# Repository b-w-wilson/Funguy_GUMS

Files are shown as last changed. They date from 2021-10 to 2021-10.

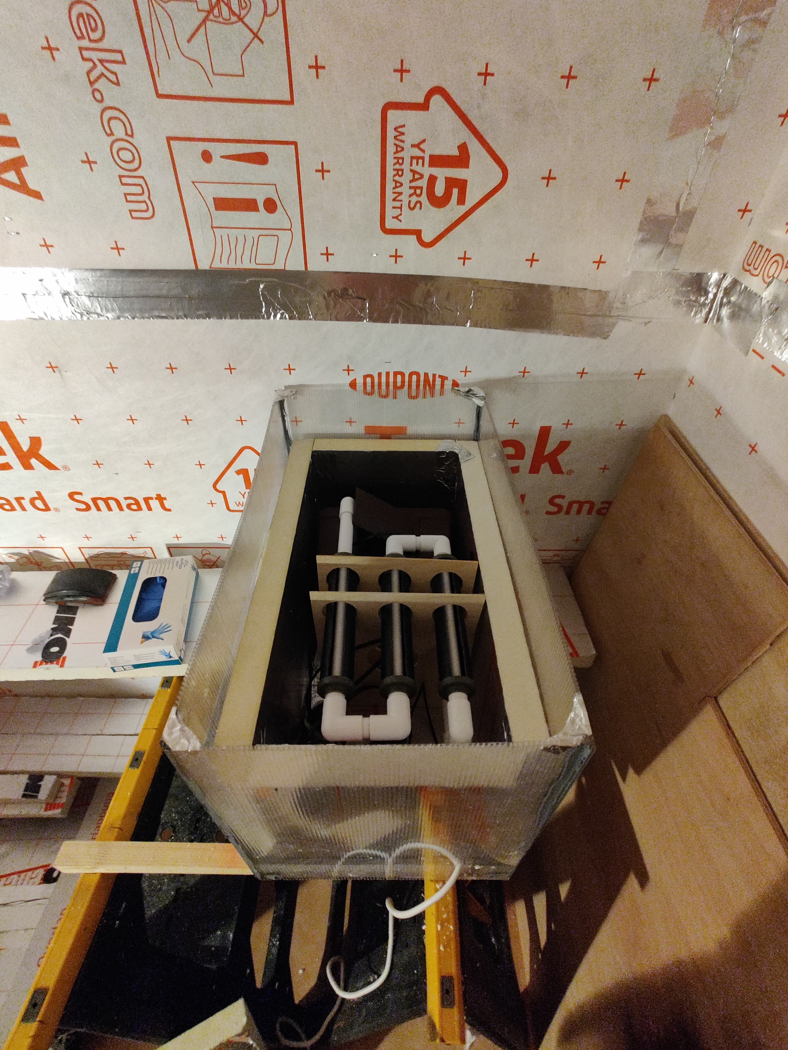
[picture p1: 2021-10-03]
Build/IMG_20211003_214133.jpg

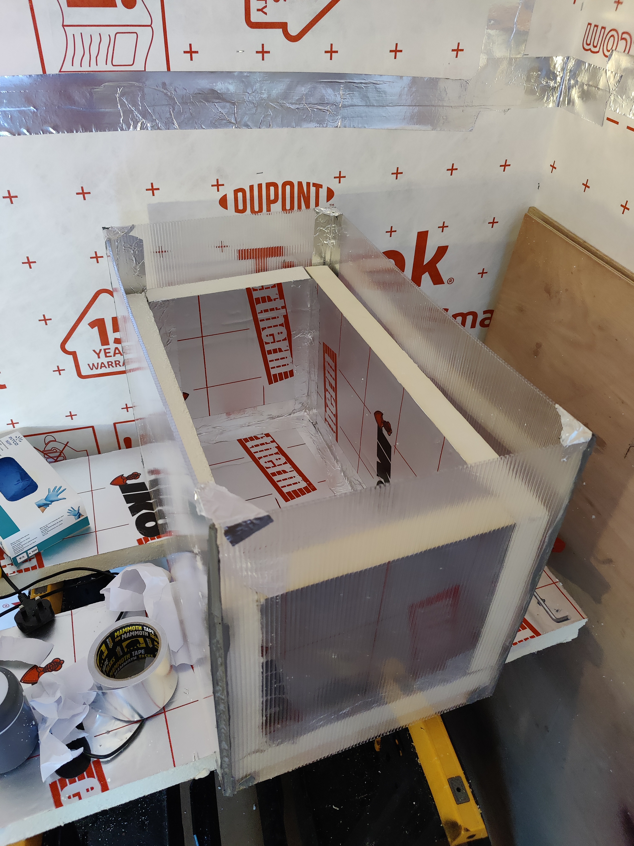
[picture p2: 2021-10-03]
Build/IMG_20211003_183508.jpg

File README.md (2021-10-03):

# Funguy_GUMS
Team Funguy final project for the 2021 NASA Space Apps Challenge Hackathon

## Exploring the solution:
* Our main solution is the "**Methods**", "**Introduction**", "**Improvements**", and "**Abstract**" documents, alongside all files in the **Build** directory.
* A CAD model was also created, with pictures in the "**CAD**" folder.
* The "**Diagrams**"" folder contains diagrams to show how our system build will work.
* References can be found in the respective "**References**" directories.
* Research conducted to create the final solution document and the build is contained in the "**Technical Design Research**" directory.
* The "**Assets**" folder contains all logos, images, or otherwise promotional material created.

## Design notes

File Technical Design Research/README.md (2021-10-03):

# NOTE:
This folder contains raw research from sources listed in our references. This is material which we used to build the actual project contained within the introduction, methods, and in the build of our system.

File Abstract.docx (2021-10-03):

GUMS: Growth Unit for Mushrooms in Space is an ingenious mushroom growing hybrid system consisting of an electromagnetically treated homogeniser for nutrient mixing and solution sanitising and hydroponic porous ceramic tubes for the nutrient delivery and recycling. The growing environment will be monitored via an autonomous sensor system, which transmits the air sensing (air temperature, relative humidity, light intensity) and water sensing (solution temperature, pH, electrical conductivity, concentration of nutrients) data to a mobile app.

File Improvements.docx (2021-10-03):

Overall, Space Apps Challenge has been a unique experience in which we have had the opportunity to grow both personally and professionally!

Over the weekend and the month prior to the challenge, we have planned out as much as possible our GUMS system and have tried to get a basic mycology background in order to better understand how mushroom growth in hydroponics based systems. We are looking forward to continuing the development by adding the additional subsystems to the main porous tube nutrient delivery system. We believe that the solution we have came up with will certainly make a difference not only in long distance space travel, but also on Earth.

Overall development of the project started with planning stage. We started with initially coming up with a few ideas of projects that we could work on, and after brainstorming some ideas around hydroponics and tomato/lettuce growth, ordered pizza. Rebeca ordered a pizza with mushrooms on it, to which Bruce responded by voicing his dislike for mushrooms. Rebeca asked what Bruce would do if he was stuck somewhere and all there were to eat were mushrooms, to which Bruce responded, “hmm.. well we could use our hydroponic system to grow mushrooms”, and there we are. With the decision made, we spent a few weeks doing background research, ensuring that on the weekend of the hackathon, we could put together our report, and build the system from scratch. Alongside this, we placed any orders of hardware or parts that they would arrive for the weekend.

On the weekend of the hackathon, we started bright and early at 9am beginning the build. First creating the growth tubes (connector ends, black ABS tube, ceramic tube), then connecting them together to the pump and nutrient tank. With a quick trip to B&Q to pick up some extra sealant and pipe 90 degree turns, this system was mostly complete, with a few worries about leaks due to how quickly it had been put together. Then on day two, the wooden base was built, along with finishing touches to the tube system. The polycarbonate encasement alongside PIR insulation was then constructed around the box, ensuring that all gaps were sealed shut with aluminium tape. Nearing the end of day two, we recorded the walkthroughs and turning on of the pump for the first time.

Our biggest challenge was faced with the heating element. Our original plan called for a 2L cola bottle to be cut and an aquarium heater placed inside, however it proved too difficult to seal once it had been opened. With some other attempts with plastic bags, cut parts of a tube, and a trip to Tesco to quickly by a cereal container in a last-ditch attempt. Unfortunately we were unable to get the heater working and in a safe, sealed environment by the end of the hackathon. Alongside this, our fears were met with reality with a few small leaks from the tubes upon the pump being ran for a few minutes. We will drain the system and fix the leaks with epoxy.

Overall, we were very content with what we have been capable to build, considering how quickly it was manufactured. It was greatly aided by the 3D printed pipe connectors and fast drying epoxy/solvent cement. While we have bought the substrate and mushroom spores in a syringe, we have yet to put the substrate in the tubes. This was due to the leaks appearing and lack of time near the end of the weekend. We fully intend on still attempting to use the system in the coming weeks.

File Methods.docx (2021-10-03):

### Growing mushrooms in space

GUMS: Growth Unit for Mushrooms in Space is an ingenious mushroom growing hybrid system idea consisting of an electromagnetically treated homogeniser for nutrient mixing and solution sanitising and hydroponic porous ceramic tubes for the nutrient delivery and recycling. The growing environment will be wirelessly monitored via an autonomous sensor system, which transmits the air sensing (air temperature, relative humidity, atmospheric gases concentration, light intensity) and water sensing (solution temperature, pH, electrical conductivity, concentration of oxygen and nutrients) data to a mobile app. Further improvements would include a treatment and dehydration stations.

Our GUMS design has been inspired by NASA’s PTPNDS system. In 2003, T.W. Draschel has published in NASA Technical Memorandum the technical design of a device which utilises a loop to control the delivery of water and nutrients to the roots of super-dwarf wheat and, subsequently, to prevent the anoxic effects experienced by plant rhizospheres in conditions of microgravity. According to the paper, eight porous ceramic tubes with a diameter of 2 cm and 80 cm length are connected to a magnetically coupled impeller at the upstream end and to a peristaltic pipe at the downstream end. These tubes are fed by a 80 litres nutrient tank attached to the upstream end whereas the solution is removed out of the system and recycled at the downstream end. Metal-halide lamps provide the necessary active radiation for photosynthesis and a bracket system is attached to diffuse the liquid nutrient solution under pressure.

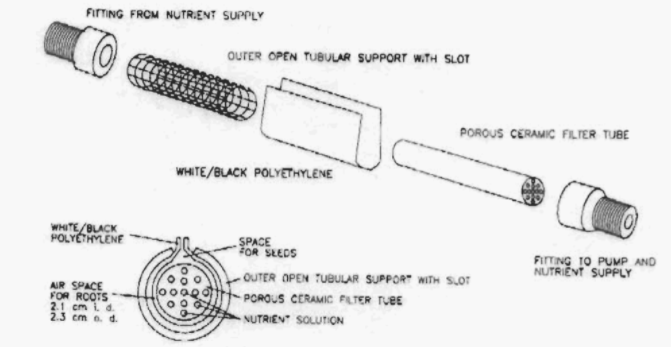
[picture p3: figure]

Fig 5: Scheme of Porous Tube Plant Nutrient Delivery System (T.W. Draschel, “DEMONSTRATION OF A POROUS TUBE HYDROPONIC SYSTEM TO CONTROL PLANT MOISTURE AND GROWTH”, NASA Technical Memorandum 2004-21 1533, October 2003)

The outline of the system is further developed by the Department of Bioresource Engineering of McGill University, Canada, in order to make it functional for mycelium and mushroom production. GUMS is a modified version of this model which uses an alignment of three porous ceramic tubes, each of 15 mm in outer diameter, 10 mm in inner diameter and 200 mm in length, rather than only one, making the system more suitable for much smaller space. If the growing chamber of McGill University’s porous tube plant for nutrient delivery system needs a 1.09 m in length, 0.59 m in width and 0.52 m in length container for the assembly, GUMS only uses 60 cm in length, 35 cm in width and 40 cm in height. Due to the reduced dimensions of the container, GUMS require less energy to be humidified and heated up, which means that we also save energy, and, therefore, money. Besides the continuous monitoring of multiple environmental parameters amongst which some uncommon ones, such as light intensity, pH and electrical conductivity, GUMS makes use of the newest discoveries in the full solution sterilizing treatments to prevent the contamination noticed in McGill University’s system and, subsequently, the pump clogging.

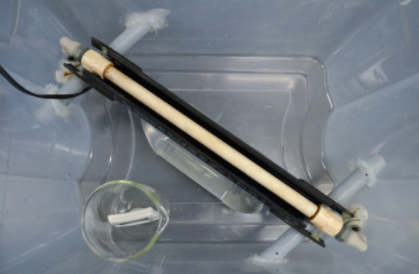
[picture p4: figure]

Figure 6: Nutrient Delivery System seen from above (Prof. Chandra Madramootoo, “Mycelium and Mushroom Production Using a Hydroponic Porous Tube Nutrient Delivery System”, Department of Bioresource Engineering, McGill University, Macdonald Campus, April 2018)

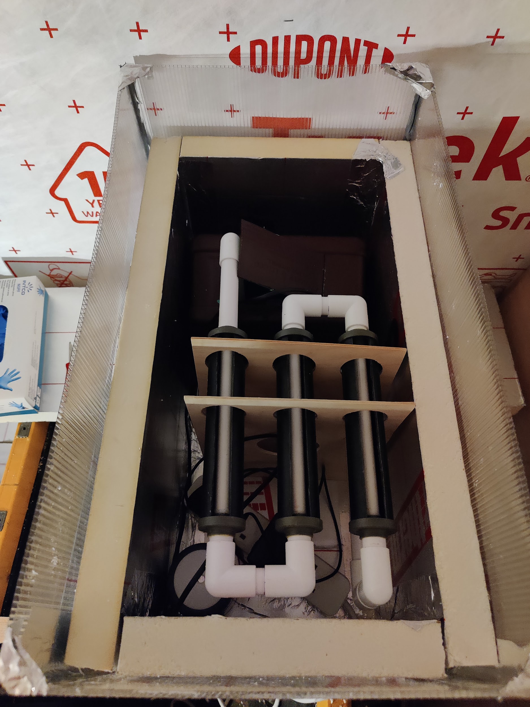
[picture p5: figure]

Figure 7: Nutrient Delivery System seen from above (GUMS design)

### Nutrient delivery system

An inert substrate of organic brown rice flour, vermiculite and gypsum was sterilized and inoculated with a liquid media containing Pleurotus ostreatus spores. The axenic nutrient solution is dispersed into a bed of nutrient free substrate, encased by ABS pipes around the ceramic tubes. The ceramic tubes are, then, joined to a 5L nutrient tank by opaque, PVC pipes. The opacity of the pipes diminish the chances of internal algal contamination. In the nutrient tank, we added a centrifugal submersible pump, attached to the nutrient tank walls using silicon caps. The remaining solution which circulated through the system is transported downstream to the nutrient tank where the consumed nutrients are replenished.

### Nutrient mixing and treatment station

From (Prof. Chandra Madramootoo et al., April 2018), we know that contamination of nutrient and water solution may be an issue, especially during the mixing. From this, we propose a system may be to mix the water and nutrient solution inside a sealed mixing chamber. This will allow for the inlet of nutrients at high pressure to mix directly with the water, creating an even distribution of components.

The homogenization will occur in a venturi space, where mechanical mixers are placed. The surface of the venturi chamber is circularly-ridged to promote further physical and chemical reactions in the aqueous media. The inlets to the chamber of the mixer as well as the nutrient tank include a jacket insulation to keep the temperatures of the liquid solutions below room temperature, and, subsequently, to increase the dissolution of oxygen and nitrogen.

In comparison with other subsystems, the venturi chamber should be treated with maximum care as there are high chances for contamination, despite UV sterilising the water before connecting to the inlet. The risk of contamination can be drastically reduced by utilising EMF solution treatment. EMF has been widely used for centuries to mitigate bacterial contamination, but also to assist the electrocoagulation and advanced oxidation processes. In comparison with electrolysis for which the presence of electrodes in the nutrient solution tank is mandatory, in the EMF treatment technique, solenoid coils are attached in the proximity of the venturi chamber to induce an electromagnetic field of high intensity and less homogeneous waveform in the liquid. Moreover, as electrodes need to be frequently checked and periodically changed, electrolysis is associated with high maintenance cost, which cannot be said about our treatment unit.

### Growth chamber

The growing chamber is our own customised polycarbonate bin, supported on a wooden base, measuring 60cm in length, 35cm in width and 40cm in height. We included the ceramic tubes inside the bin whereas the nutrient mixing and treatment station is kept outside the bin. The openings cut in the polycarbonate sheets to connect the subsystems have been surrounded by flexible silicone adhesive in order to forbid the air flow transfer between the bin and the outer space. The stability of the ceramic tubes is given by plastic fittings. The whole chamber is surrounded in 40mm PIR insulation to trap heat and moisture inside and reduce the energy requirements of the system.

### Heating system

The heating system comprises a 2L soda bottle, partially filled with water in which an aquarium heater is glued with silicone adhesive. The heater has incorporated a thermostat so as we are able to change the temperature to accommodate different growing stages. Currently, as our system is in the mycelial growth stage, we keep the temperature higher, at 25 degrees Celsius and the humidity at 85%.

### Wireless environmental monitoring

To monitor the environment around our system, alongside the environment inside our system, we propose that a series of sensors could be used to monitor all aspects of the fungi growth. This system would be controlled by a central computer, which would receive many inputs from sensors, and output the calculated result to the actuators.

The air parameters FUNGUY decided to monitor are air temperature, relative humidity, atmospheric gases concentration, light intensity. The light is provided by a 4.5W 2700K LED bulb. The state of the nutrient solution is communicated by water sensors, such as the solution temperature, pH, electrical conductivity, and concentration of oxygen and nutrients.

These sensors should be wireless, enabling a clean wire-free connection from inside each individual growth chamber, to the main monitoring computer. Alongside this, the actuators would also be wireless. These actuators would be pump output, humidifier output, heater output, and LED bulb output.

### Modular design

GUMS has been designed to sit on two rails and be rack mounted. At the back of the bin there is a input/output port, allowing for power inside the chamber alongside nutrient solution to be filled. If for any reason a GUMS unit fails, it can be quickly swapped out with a functional unit to ensure that enough food is continuously being grown onboard the craft. A system failure would automatically be noticed by the wireless environment monitoring, and personnel would be notified via the mobile app that a unit has malfunctioned.

### State Machine Diagram

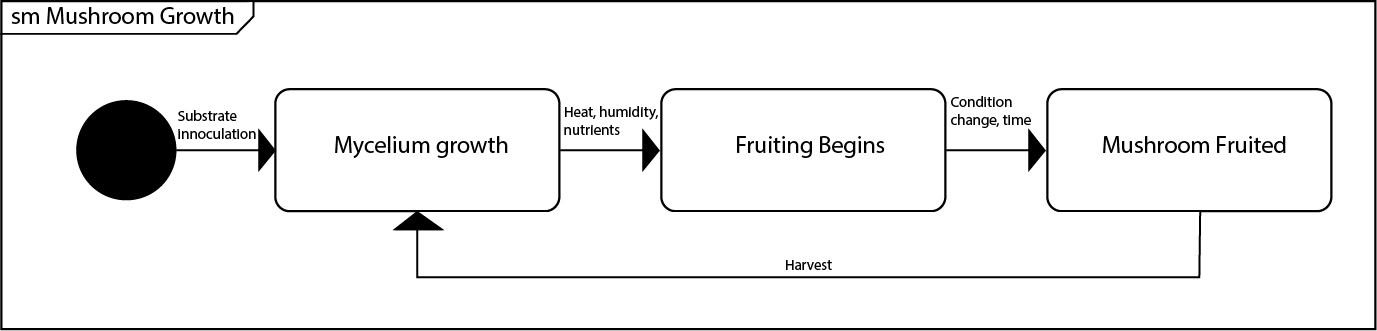
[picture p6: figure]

## System Architecture

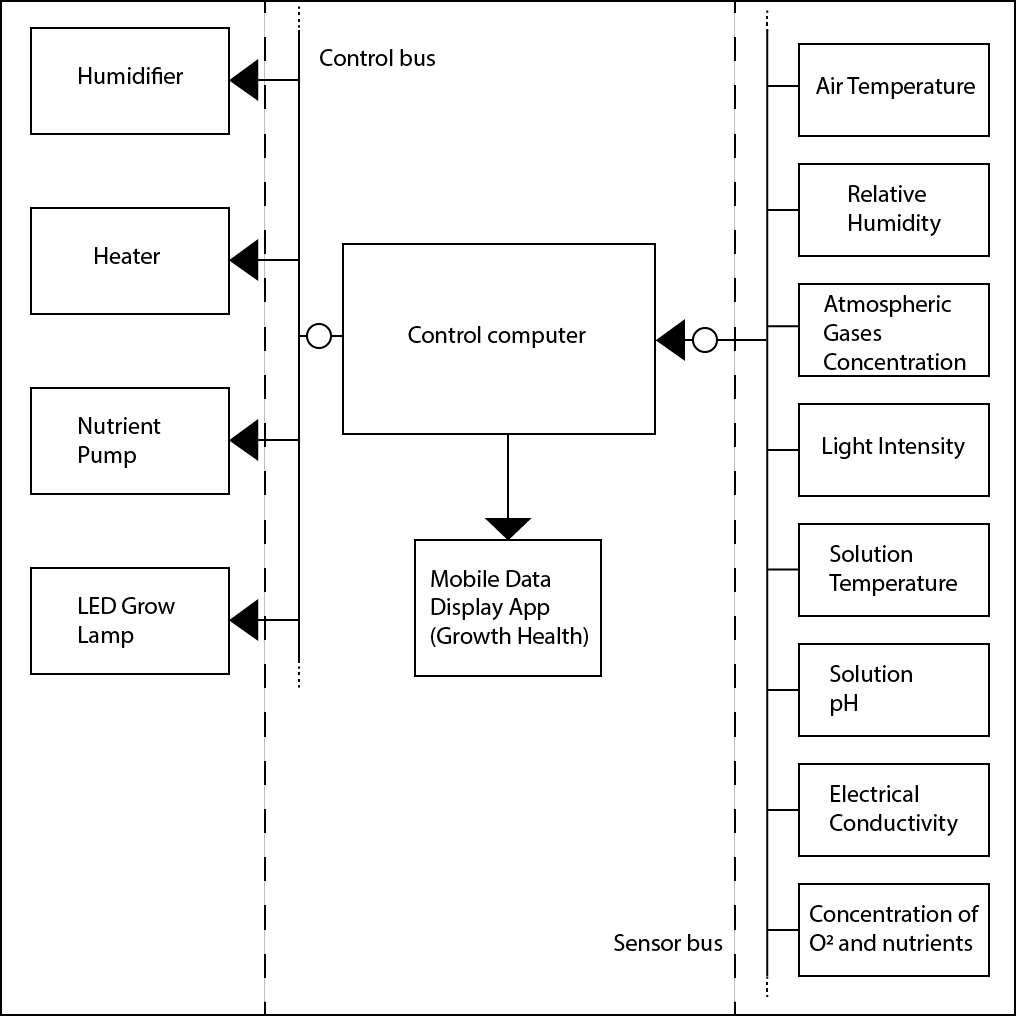
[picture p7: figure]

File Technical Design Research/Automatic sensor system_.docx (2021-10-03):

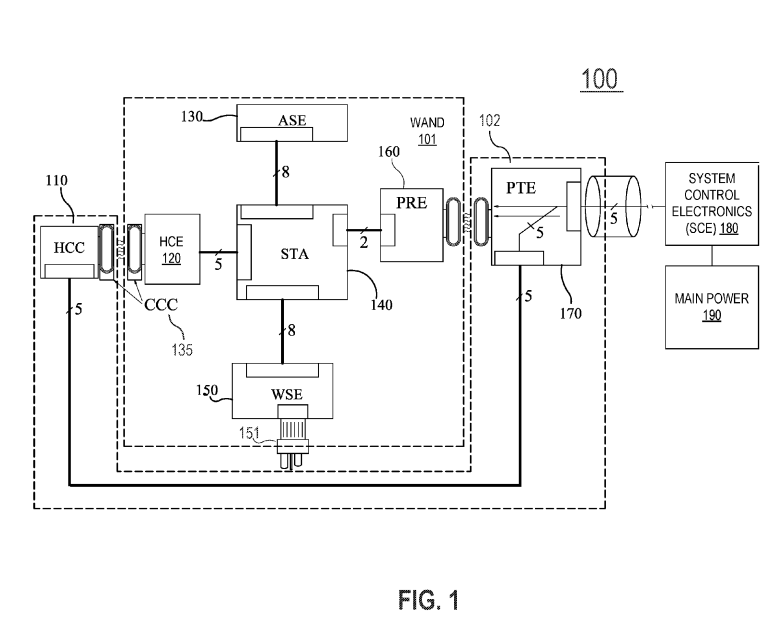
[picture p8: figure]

101 = WAND

102 = collar

120 = H-Field Communications Electronics (HCE)

130 = Air Sensor Electronics (ASE)

140 = Station Board (STA)

150 = Water Sensor Electronics (WSE)

160 = Power Receiver Electronics (PRE)

110 = H-Field Communications Collar (HCC)

170 = Power Transmitter Electronics (PTE)

- PTE employs power, ground, and data lines connected to System Control Electronics (SCE)

190 = main power supply

- power supply may be or connect to a line Voltage from a power company and may be transformed or rectified in different ways to power SCE and other Subsystems
- SCE and main power supply may connect to WAND, for example, to communicate information through with or through WAND and collar system
- PTE in an exemplary implementation provides power to PRE, which may be inside a housing of WAND, and PRE distributes power within WAND to HCE, ASE, STA, and WSE

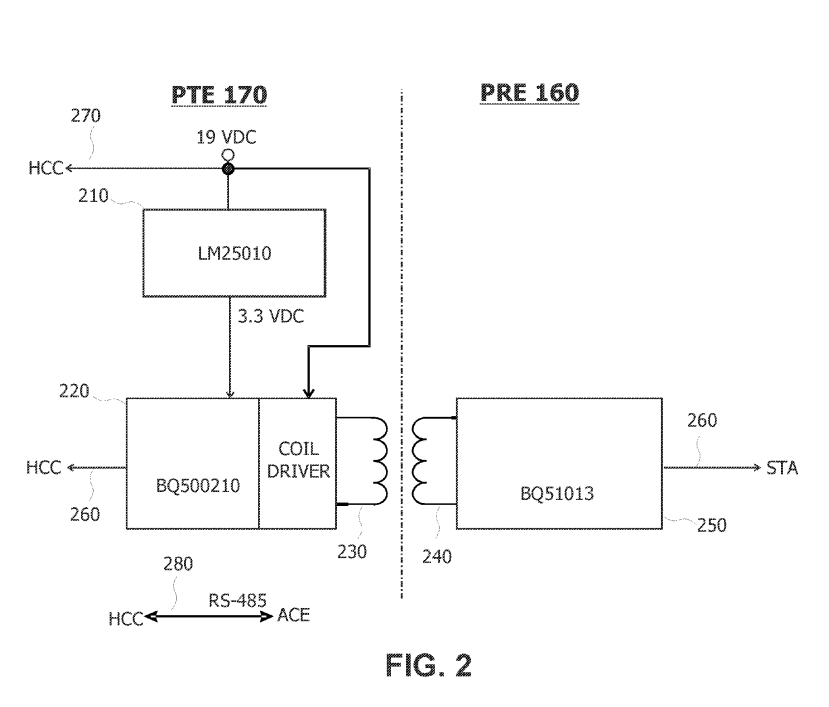
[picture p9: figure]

210 = regulator

- receives 19 VDC from an external supply
- provides a 3.3 VDC output to power a manager

220 = manager (eg Texas Instruments P/N BQ500210 “Qi Compliant Wireless Power Transmitter Manager )

- provides a pulse width modulation (PWM) drive signal to a high speed coil driver (eg Texas Instruments TPS28225) which in turn drives a transmitting coil

230 = Wurth Wireless Power Charging Transmitter Coil

- Uses 19-VDC supply
- In the proximity of a receiving coil

240 = receiving coil (eg TDK P/NWR-483250)

- electrically connected to a Texas Instruments BQ51013 Wireless Power Receiver

250 = Texas Instruments BQ51013 Wireless Power Receiver

- 5.0 VDC output of the power receiver may be provided to STA 140 on a line 260

5.0-VDC power received by STA 140 from PRE 160 on line 260 is further provided directly to the HCE 120 on a line 343, WSE 150 on a line 342, and ASE 130 on a line 341. 5.0 VDC power is converted to 3.3 VDC and provided to a Wi-Fi unit

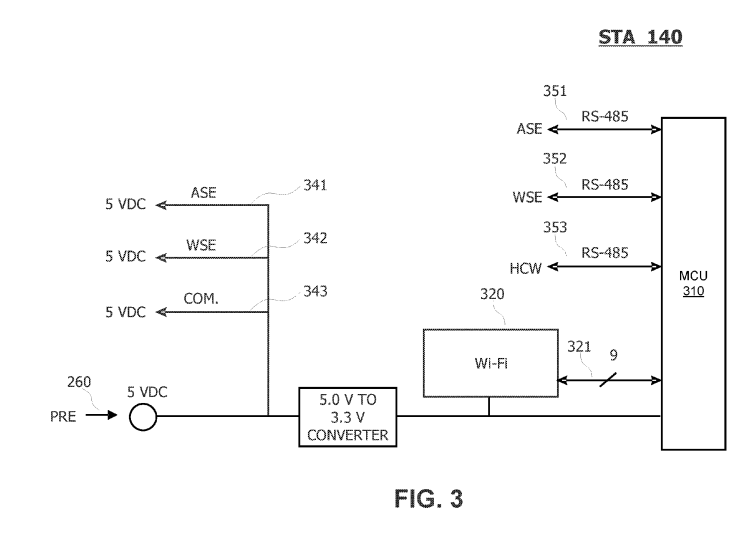
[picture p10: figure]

320 = Wi-fi unit (eg a Microchip MRF24WGOMA)

- responds to data and commands provided by a microcontroller unit

310 = microcontroller unit (eg Microchip PIC32MX695F512L)

STA 140 may also include RS-485 communications capability between MCU 310 and ASE 130 on a bus 351, WSE 150 on a line 352, and HCE 120 on a line 353.

ASE

- STA 140 may connect to ASE 130, which may support a Suite of sensors for sensing characteristics of the environment of a growing plant. In addition to power and ground on line 341, STA140 may have an RS-484 communications for wire, two-way communication with ASE 130 via bus 351.
- sensors that measure concentrations of CO, CO. and O in the atmosphere around a plant and sensors that measure characteristics of the ambient light in the environment.

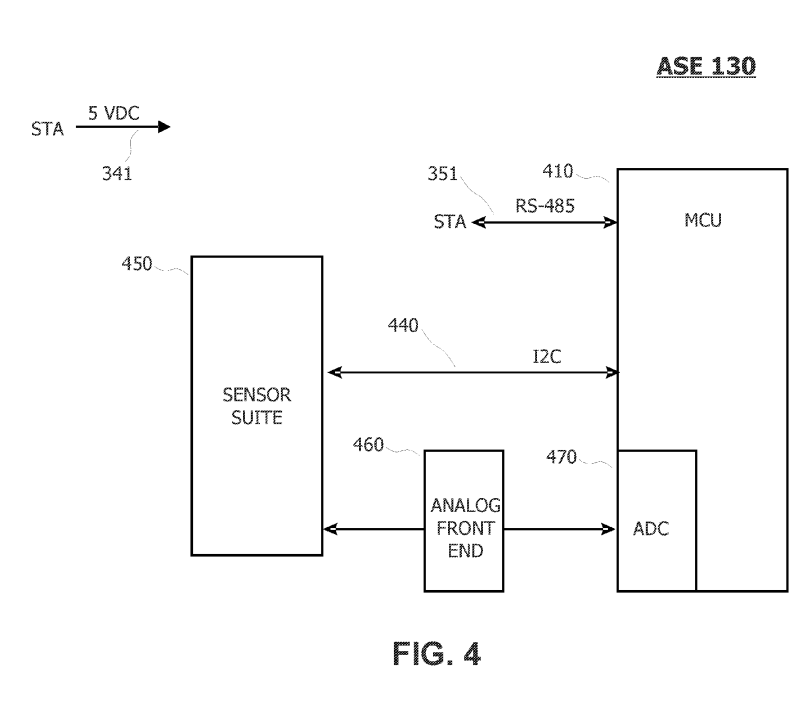
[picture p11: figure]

- ASE 130 may include an MCU 410, for example, a PIC32MX350F256H microcontroller, wherein MCU 410 includes an analog-to-digital converter (ADC) 470
- MCU 410 may manage the sensors, for example powering them up or down, placing one or more sensors in standby or operative mode, determining the status of one or more sensors, or performing diagnostics on one or more sensors.
- MCU 410 may also be programmed to receive requests for data related to a given sensor and to provide the data back to STA board 140 via the RS-485 bus 420
- STA 140 may then provide the data to the requester via the Wi-Fi unit 320 or another data link.

WSE

- Principle of working identical to ASE 130
- Examples of sensors include any c combination of pH sensors, temperature sensors, total dissolved solids (TDS) sensors, sensors of specific chemicals, resistivity sensors, and any other sensors useful for sensing one or more characteristics a nutrient Solution in a hydroponic system

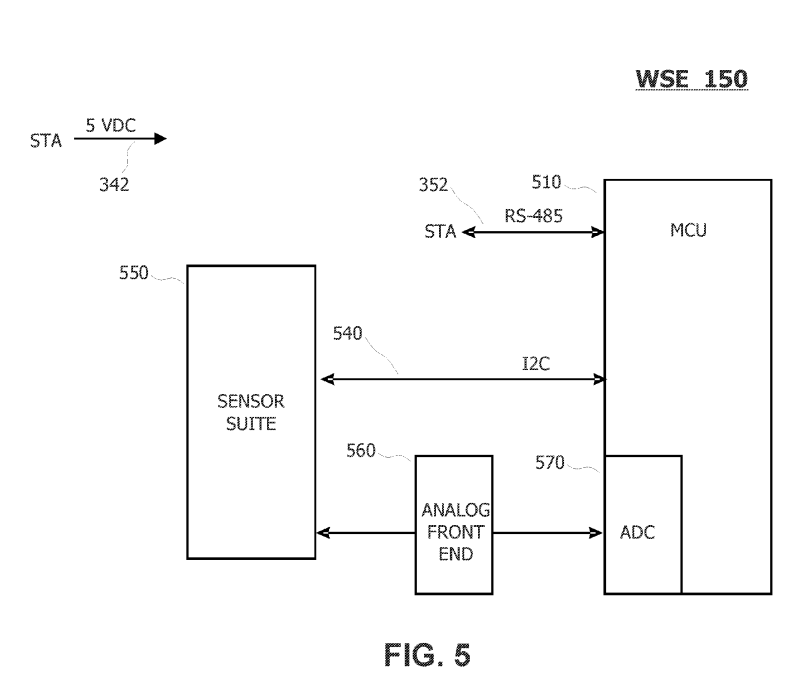
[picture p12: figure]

HCE

- HCE 120 and HCC 110 operate in a similar fashion to PTE 170 and PRE 160, except data is exchanged between the transmitting and receiving coil rather than power.

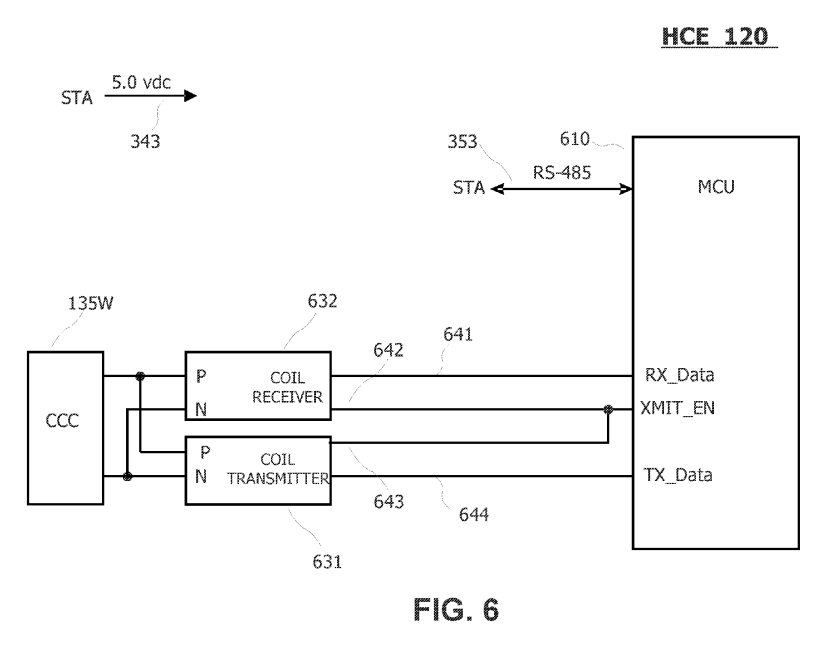
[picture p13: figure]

- MCU 610, for example, a Micro chip PIC32MX350F128D, may communicate with STA 140 via the RS-485 bus 353.
- MCU 610 receives data on a line 641 and sends data on a line 644.
- Data activity is controlled by an enable signal XMIT EN on a line 642, 643.
- signals connect MCU 610 to a coil transmitter 631 and a coil receiver 632.
- P and N signals from the coil transmitter 631 and the coil receiver, connected to drive a coil, e.g., a CCC

CCC 135W coil interacts with a matching (may be identical) coil CCC 135C on HCC 110, the pair of coils being proximate to enable inductively passing data signals when the WAND is inserted for operation.

HCC

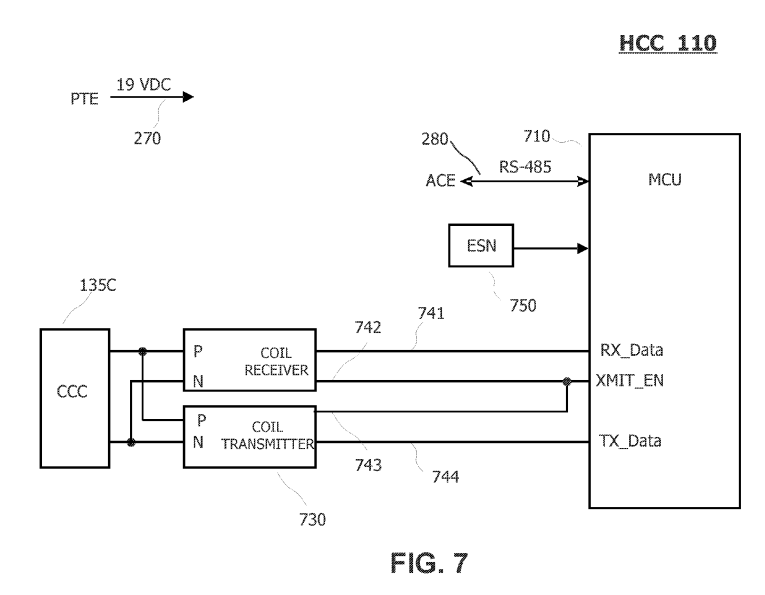
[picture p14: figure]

- Similar in working as HCE
- communicate with SCE 180 via the RS-485 bus 280
- HCC 110 includes an ESN (electronic serial number) (eg a Maxim Integrated DS2411)

SCE

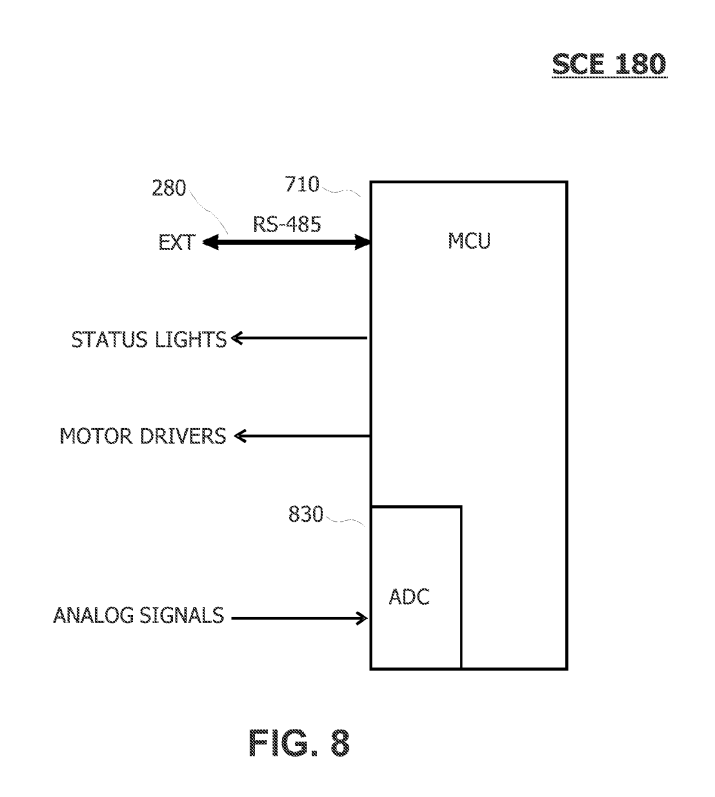
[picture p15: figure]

- communicate with WAND 101 via HCC 110 on an RS-485 bus 280
- include an MCU 810, which includes a number of general purpose input/output (GPIO) pins 820.
- include an ADC 830 to provide a digital version of analog signals connected to the ADC 830
- MCU 8.10 may provide signals to turn fans ON or OFF, and turn on a light of an appropriate color
1. Implementation of network station
- includes a microcontroller 1210 that may be programmed for desired communications among sensor modules 1130 and 1150, system control 180, and through a network to a remote device
- controller 1210 may execute software or firmware to collect data points from ASE module 1130, WSE module 1150, or system control electronics 180, to upload the data points to a remote device or cloud database, and to provide system control electronics 180 with the data points or with data, commands, or instructions received from a wireless network.
- Controller 1210 connects to an ASE interface 1230, which may be a chip or other electrical circuit that implements a signaling protocol to transmit or receive communications with ASE module
- ASE interface 1230 may be RS-485 compliant and may connect to ASE module 1130 through a connector 1232

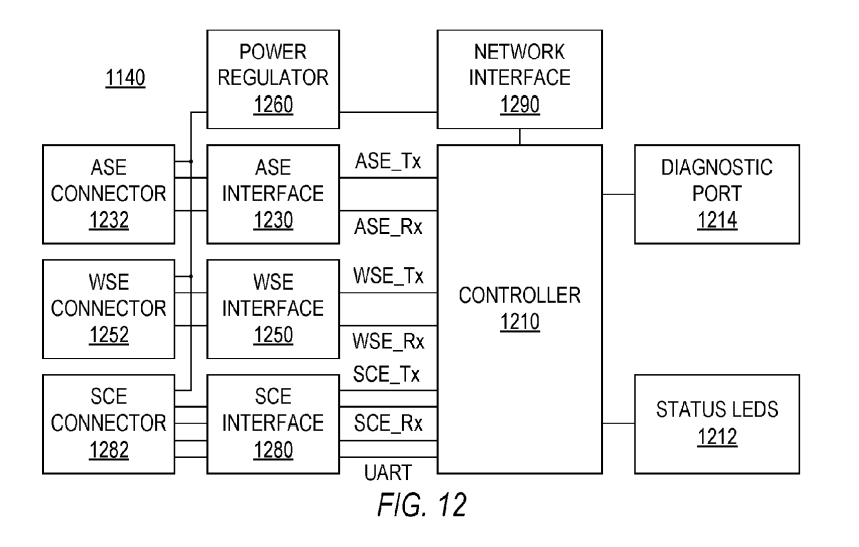
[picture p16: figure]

- controller 120 connects to WSE interface 1250 and SCE interface 1280, which respectively allow wired communication with WSE module 1150 and system control electronics 180 through respective connectors 1252 and 1282
- power regulator 1260. which provides power to controller 1210 can also provide power or receive power via connectors 1232, 1252, and 1282 to ASE module, WSE module 1250, and system control electronics
- A network communication interface 1290 may be a chip or electronic circuit that implements a wireless protocol, e.g., Wi-Fi, that enables network device 1140 to communicate through a wireless network
2. Implementation of sensor electronics
- includes a controller 1310 that may be programmable to operate, receive measurements from sensors, and transmit the measurements to network station 1140.
- sensors 1350 may be able to digitally communicate with controller 1310 or may provide analog measurement signals to an analog frontend 1352 that converts the analog signals to digital signals suitable for controller 1310.
- Controller 1310 may communicate information such as sensor measurements to network station 1140 through an interface circuit 1340 such as an RS-485 compliant interface chip connected to network station 1140 through a connector 1242
- power regulator 1360 is used in the implementation to receive power through the connector and to supply regulated power in ASE module 1130.

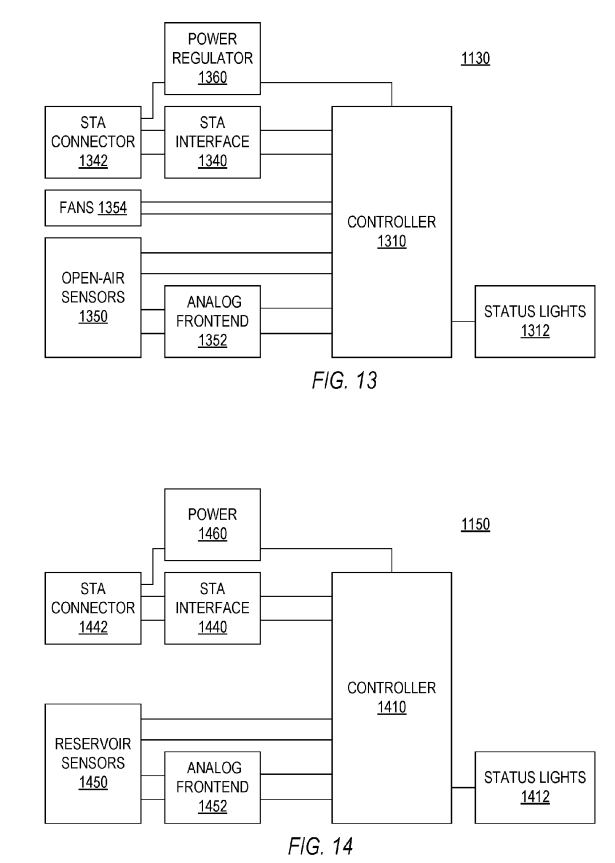
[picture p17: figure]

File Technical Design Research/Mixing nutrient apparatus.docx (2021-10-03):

1. HYDROPONICS APPLICATIONS AND ANCILLARY MODIFICATIONS TO A POLYPHASIC PRESSURIZED HOMOGENZER
a) Introduction
- Ancillary embodiments and modifications to a homogenizer unit (“PPH'), and methods of use directed to hydroponics.
- The apparatus includes a homogenizer body, one or more nutrient stream inlets, one or more water inlets, a mixing Zone where the water stream is commingled with the nutrient stream, and a venturi within the body immediately down stream from the mixing Zone such that the commingled streams are pulled into the Venturi resulting in homogenization.
- The PPH components are insulated to maintain the aqueous nutrient Solutions cooled, below ambient temperature.
- The resulting aqueous nutrient solution can be conveyed in its cooled State to roots of hydroponically grown

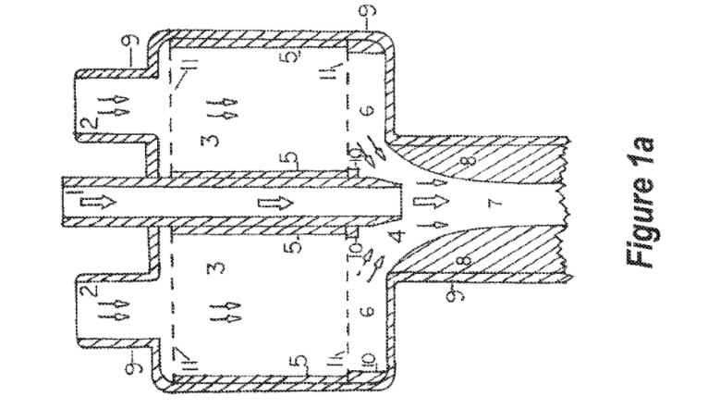
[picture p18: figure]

b) Description
- modified homogenizer unit includes an integrated unit having a much expanded housing that is intended to contain a replaceable ante-mixing chamber containing various packings, baffles, and/or sorbents.
- The housing (9) also has top mounted ports.
- The central port (1) is dedicated to the input of water or a similar solvent mixture.
- One port or several ports (2) is/are dedicated to entry of a gas, gases, liquid, liquids, any type of particle or mixture of particulates that will pass through the port, the ante-mixing chamber or mixing chamber,
- The components are numerically identified as it follows:
1) water or other solvent intake port and jet or nozzle
2) pollutant stream port or ports
3) ante-mixing chamber
4) mixing chamber
5) ante-mixing chamber housing
6) lateral extent of mixing chamber
7) venturi throat
8) Venturi
9) homogenizer housing
10) ante-mix chamber support
11) ante-mixing chamber screen Supports.
- Headspace modifications or embodiments may include a mechanical mixer, mounted on a shaft, driven by an electric motors
- The solution enters the headspace region by one or more ports by passing through a perforated bulkhead, that is mounted within the homogenizer housing
- A single transfer tube or line allows for passage of a solution into the headspace of the homogenizer
- Mixing may be done by a mechanical mixer or by casual mixing while flowing into the ante-mix chamber. This port(s) may be positioned on the homogenizer housing or one or all intake ports other than water
- ante-mix chamber may be cylindrical in structure and fit tightly within the ante-mixing chamber and directly superior to the mixing chambers of the homogenizers
- ante-mixing chambers depicted include the exterior housing, the interior housing the top and bottom support screens
- ante-mixing chambers are Supported both laterally and centrally by circular ante-mixing chamber Supports
- perforations in the upper and lower screens of the ante-mixing chambers may have a variety of designs ranging from hexagonal, circular, square, to diamond-shaped
- These perforations allow for circulation of gas through them while containing and Supporting the various packings within the chambers
- These packings are varied in configuration and may be Bioballs or any other similar configuration, baffles, having any configuration, cross-section, and Surface treatment
- Water and a solvent or solvents containing water and another reactive chemical is delivered to the mixing chamber by a jet or jets
- homogenizer unit mixing chamber is positioned between the jet(s) and above the Venturi(s) of the homogenizer unit(s)
- Although the boundaries of this mixing chamber are not well-defined, this region is the uppermost area wherein the solvents begin to mix before entering the throat
- It is within the venturi that the solvents come into intimate contact with each other
- smooth venturi surface is one option, while a circularly ridged or grooved surface, a surface with vertical vanes allows for furthering certain reactions, and a radially-grooved surface can be used.
- Mixture continues in the retention chamber which may have a series of spherical chambers, be baffled, have a centrally located spiral conduit, or the serial spherical chambers may have a centrally-located spoiler ball or bead
- the extreme lower end of the retention chamber has four, equi-spaced lateral discharge ports.
- These ports can be produced into tubular form, or continued on to form a j-tube
- result in the increase of safety margins by containing the chemical and physical reac tions within an aqueous medium, thereby both containing out-gassing and heat generation from exothermic reactions while also cooling any such reaction by rapidly diluting the reactantS.
- One embodiment is directed to apparatus and methods that may be employed for introducing nutrients into a water stream to provide an aqueous nutrient Solution for hydroponics plant growth
- Such a PPH apparatus may be any of those configurations described herein, and in one embodiment may further include an insulated jacket around Such components as the inlets, the ante-chamber, the venturi, and the outlet to maintain the nutrient solution at temperature below ambient temperature so as to increase dissolution of oxygen, nitrogen, or both into the aqueous nutrient solution. Where a retention chamber is provided within the PPH, it of course may also be insulated.

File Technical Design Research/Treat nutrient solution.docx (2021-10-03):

1. ELECTROCHEMICALLY TREATED NUTRENT SOLUTIONS
- Nutrient compositions with preservative properties are of great need for a variety of agricultural applications, such as,for example, hydroponics where oxygen deficient media results in favorable conditions for undesirable microbial growth, as well as for pre-harvest and post-harvest crop maintenance.
- However, it is critical that the preservative constituents of the composition do not interfere with plant growth, development, and/or quality.
- Free oxygen radicals, for example, which may have biocidal activity, can underlie basic plant signaling and stress responses
- invention provides nutrient compositions that are oxygen-enriched, and potassium-based.
- In literature, the nutrient composition comprises a solution that is generated through electrochemical treatment of potassium chloride or a combination of potassium chloride (KCl) with potassium or sodium carbonate or bicarbonate (KCO, NaCO, KHCO, NaHCO), or other carbonate salt, and/or potassium phosphate(s).
- feed solution may be processed through an electrolytic cell to produce an electrochemically-treated solution
- The solution produced by electrochemical treatment has a predetermined salinity level, pH and concentration of oxidants measured as free available chlorine
- the nutrient composition or solution is used to support hydroponic plant growth.
- for example, the nutrient solution either alone or in combination with other active ingredients are cycled continuously or intermittently through a hydroponics system. The disease protection and/or enhanced plant growth, development and/or health realized by using the compositions and methods of the present invention may lead to improvements in plant performance including but not limited to obtaining greener plants, greater yield, better standability, less root lodging and/or less fruit rotting.
- invention provides a method for preparing the oxygen enriched potassium-based nutrient solution or composition for supporting plant or crop production.
- The method involves incorporating carbonate or bicarbonate (as described) into KCl electrolyte for electrochemical treatment, or directly to an electrolyzed solution of KCl comprising hypohalous acid (e.g., HOCl).
a) Description
- provides nutrient compositions that are oxygen-enriched, and potassium-based, and comprise hypochlorous acid and potassium salts
- composition promotes plant or crop growth through various stages of development, and/or reduces or eliminates the risk of airborne and waterborne anaerobic bacteria, as well as mold and fungal diseases
- combination of oxygen and hypochlorous acid pro vides antimicrobial properties to the nutrient composition, and in combination with potassium, induces systemic protection and modifies disease resistance or susceptibility of crops to infections
- composition is based on a solution prepared by electrochemical treatment of a KCl solution with one or more (or all) of KHCO/KCO, NaHCO, KPO KHPO, and KHPO.
- Other electrolytes, or salts may be included as well as additional ingredients desired
- The feed solution may be processed through an electrolytic cell to produce the electrochemically-treated solution.
- A diaphragm-based electrolytic cell, may be used for the electrochemical treatment; however, other electrolytic cells with separated anode and cathode chambers may be employed.
- For example, the Sterilox(R 2200, or SteriloxR 2300 may be used for the electrochemical treatment.
- The solution produced by electrochemical treatment has a predetermined salinity level, pH, and concentration of free available chlorine (AFC).
- As a result of the electrochemical process of KCl alone or with the addition of the salts (as described), diluted (i.e., below 1.5 g/L of total dissolved solids) nutrient solutions with targeted pH and total oxidants, measured as AFC, are produced.
- The solution in certain embodiments, employs a stabilizing amount of a bicarbonate or carbonate of alkali or alkaline earth metal. Such as, for example, Sodium, potassium, calcium, or magnesium.
- the solution is considered stabilized if the amount of AFC does not drop below about 75% of the initial value over a period of about 6 months.
- The nutrient compositions or solutions may be applied bya foliar spray to the plants in the hydroponics system. either separately or mixed together with other active compounds
b) Example
- A mixture of 2 g/l of KHCO and 8 g/l of KCl were used as a feeding electrolyte solution processed through the diaphragm based electrolytic cell. The final nutrient solution had
- a pH 5.8, electro-conductivity 1.88 mS/cm, oxidants content of 500 ppm (measured as available free chlorine), and 208% saturation of dissolved oxygen.

2. LIQUID TREATMENT DEVICE

- A liquid treatment device comprising : two antennae ; an enclosure for holding a liquid including a solvent and a solute ; a generator operatively connected to the two antennae to generate an oscillating voltage in each antenna , wherein each voltage is out of phase with the other to create an oscillating electric - field ; and the liquid in the enclosure being subjected to the electric - field in the presence of a magnetic field to change the chemical and / or physical prop erties of the solute , without the liquid contacting the two antennae .
- agriculturalists often use borewater / groundwater 35 atomic / molecular mass of that solvent or solute ; and sources that contain high levels of minerals such as calcium carbonate , magnesium carbonate , and sodium chloride
- These borewater / groundwater sources may be used to field the water crops or livestock
- However , carbonates precipitate chemical and / or physical properties of the solute , without over time , producing scale, which may clog the irrigation
- deleterious effect of the precipitation is the reduction in concentration of minerals in the borewater for crops to absorb .
- In agricultural industries , mineral nutrients such as calcium , phosphorous , potassium , sulfur , sodium , solute . chlorine and magnesium required for their growth
- Electrolysis has been used to improve the solubility of combined magnetic field . minerals in solution . However , this technique requires the use of electrodes to treat the water .
- This can be difficult to implement as it requires access to the water such as through portholes cut into existing pipes to insert the electrodes into the water .
- Furthermore , the electrodes would have to be monitored and periodically replaced , which increases maintenance cost
- antennae are electrically isolated from the liquid
- the antennae can be wrapped around a pipe containing the liquid to be treated , whereby the pipe electrically insulates the antennae from the liquid
- antennae do not include electrodes that have to contact to treat the liquid
- generator may generate one or more frequencies to target one or more solutes
- The frequency is proportional to the magnetic field strength B
- frequency may be controlled by the generator by first converting mains alternating current ( AC ) to direct current ( DC ) , before generating voltages of particular frequencies .
- As such , the frequencies output by the generator are not a function of the mains AC frequency
- generator may be powered by a DC power source , such as for example , a solar DC power source to generate oscillating voltages
- the frequency of the oscillating voltage in each antenna is a harmonic of the fundamental frequency of a solvent or solute , and is calculated using the cyclotron resonance harmonic formula :

f_(n+1) =(n+1)Bq/(2πm)

,wherein fn + 1 is an overtone of fundamental frequency , B is the magnetic field strength , q is the solvent charge , solute charge or solvent dipole charge , m is the atomic / molecular mass of the solvent or solute and n equals zero or any whole number

- In cases where n = 0 , the cyclotron resonance harmonic formula reduces to the cyclotron resonance formula
- frequency of the oscillating voltage in each antenna may be calculated using the cyclotron resonance formula

f=(Bq)/(2πm)

wherein scalar f is the frequency of the electric field modulation , scalar B is the magnetic field strength , scalar q is the solvent charge solute charge or solvent dipole charge , and m is the atomic / molecular mass of the solvent or solute

- the liquid treatment device may include a power supply , a means of estimating or measuring magnetic field strength and a calculator for calculating an oscillating voltage to generate an oscillating electric field , wherein the generator uses the power supply to generate the oscillating electric field
- means for estimating or measuring a magnetic field strength is a magnetometer
- device may further include a controller for carrying out any one or more steps of : receiving a signal that conveys the magnetic field strength , calculating a frequency of the oscillating electric field based on magnetic field strength , and sending a signal to the generator to generate the oscillating electric field using the power supply
- liquid may be subjected to an agitation force that is a function of electric field strength , magnetic field strength and instantaneous velocity of an included solvent or solute particle
- controller may carry out any one or more steps of : the selecting an agitation force , estimating or measuring a magnetic field strength , selecting a frequency for an oscillating electric field based on the agitation force selected and sending a signal to the generator to generate the oscillating electric field using the power supply
- liquid is subjected to an agitation force calculated using the Lorentz force formula

F = |g|[E+(ν×B)]

where B is comprised of the instantaneous strength and direction of the magnetic field

q is the solvent charge solute charge or solvent dipole charge

E is comprised of the strength and direction of the alternating electrical field alternating at any frequency

v is instantaneous velocity ( comprised of speed and direction ) of an included solvent or solute particle

F is the force acting on a charge q when q moves within coexisting electrical and magnetic field

- the controller may be used for calculating the frequency of the electric field based on the magnetic field strength obtained from the magnetometer
- the calculations using the cyclotron resonance formula or the Lorentz force formula individually made for each solvent, may be used to calculate the agitation force acting on a charge q when q moves within coexisting electrical and magnetic field
- According to the invention , the liquid is subjected to the electric - field in combination with either the vector magnetic field B or scalar magnetic field B , to increase solubility of the solute in the liquid
- The same oscillating voltage frequency may be supplied to each antenna .
- voltage may be generated as a modulated DC wave-form
- voltage may have a sinusoidal or square waveform in each antenna
- magnetic field value in the cyclotron resonance formula or Lorenz curve formula may comprise the Earth’s magnetic field at the treatment location or the summation of all magnetic field sources (including Earth’s)
- Antennas should be in contact with the enclosure in which the liquid is hold
- lowest frequencies used by the liquid treatment may be about fifteen - fold lower than the fundamental cyclotron resonance frequencies for a solute or solvent
- highest frequencies used by the liquid treatment device may be about one - thousand - fold higher than the fundamental cyclotron resonance frequency for a solute or solvent
- antennae have little or no appreciable current flow as the electric - field is generated by creating a voltage difference between the two antennae
- e oscillating electric - field frequency may be between 0.3 Hz to 300 kHz
- voltage waves may be 180 ° out of phase with each other
- oscillating electric - field:

( i ) a first continuous emission

( ii ) a frequency change

( iii ) a second continuous emission that continues for a period ranging from 1 millisecond to 10 seconds

- Frequency shift is followed by a series of additional frequency changes with each new frequency persisting for a period ranging from 1 millisecond to 10 seconds
- liquid treatment device may include a magnetic field coil as a source of magnetic field .
- The magnetic field coil may be a closed coil ( part of a closed circuit ) and generates an electromagnetic field
- voltage in the magnetic field coil is a modulated DC waveform which is in the same phase as the waveform in one of the antennae
- magnetic field coil may be positioned between the two antennae
- magnetic field coil , if present , may be in the form of wires that can be wrapped around a liquid - containing enclosure
- At least some portion of the magnetic field may be oriented perpendicular to the electric - field .
- This may maximise the force generated to aid dissolution of the solutes in the liquid
- magnetic field coil produces a magnetic field having a strength that ranges from 1/100 to 9/ 10 of the Earth's magnetic field strength ( 1 uT to 200 uT)
- generator may employ an algorithm that utilises a set of frequencies in alternating and / or sequential fashion over a period of time

Example

- Growth of lettuce in hydroponics
- Cyclotron resonance formula was used to specify particular frequecies for the LTD , targeting particular solutes and solvent
- Water treated by UV before being added to the solution
- A digital CR frequency generator ( circuit board ) was used to set up a modulated electrical field to treat the hydroponics medium
- During plant growth , the electrical conductivity and pH of each treatment solution was adjusted as required

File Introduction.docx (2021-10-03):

Growing food in conditions of microgravity has been a matter of interest for the scientific community for a long time, mainly because our dream to conquer outer space can only be accomplished if the basic human needs are satisfied.

### Pleurotus ostreatus and its mycological characteristics

Currently, there are at least 12,000 species of mushrooms worldwide out of which 2,000 species are reported as edible and only 35 are commercially cultivated, with Agaricus bisporus being the most popular. In this project, we have decided to cultivate Pleurotus ostreatus by considering the time of growth and the availability of mycelium on the market. Known as oyster mushroom, Pleurotus ostreatus is a common saprophyte species of the basidiomycetes group, one of the two main large divisions which form the subkingdom Dikarya within the fungi kingdom. As the name suggests, the species has an offset, tongue-, spatula-, or oyster-shaped pileus spanning 2-30 cm. The colour of the pileus can vary between different shades of grey. The pileus is supported by a short, whitish, eccentric or lateral stripe, and, therefore, its thickness depends on the stripe arrangement. White or cream lamellae occur on the decurrent hymenium whereas the white to lilac-grey spore print shows 8-12 μm ⨯3-4 μm sized, hyaline spores.

In the natural environment, Pleurotus ostreatus thrives on the living or dead parts of plants in temperate and subtropical forests during autumn and winter times, when the temperatures are up to 15℃. High carbon dioxide concentrations, up to 28% of the volume, stimulate the growth.

### Mushrooms as an ideal source of nutrients

Either on Earth or in space, a balanced nutrition is crucial in providing the organisms the necessary minerals to maintain high energy levels and, subsequently, good health.

Since antiquity, the fructification of higher fungi has been an integral part of the human diet as it is easily seen with the naked eye, picked by hand, and consumable without processing. The reason for which mushrooms are appearing more and more frequently on our plates is because they represent are source of variety of nutraceutical compounds such as polysaccharides (β-glucans), dietary fibres, terpenes, peptides, glycoproteins, alcohols, mineral elements, unsaturated fatty acids, antioxidants like phenolic compounds, tocopherols, and ascorbic acid. Moreover, the bioactive compounds have proven effects on strengthening the immune system and prevention of heart diseases, hypertension, cerebral stroke and cancers. Mushrooms are also known to exhibit antifungal, anti inflammatory, antitumor, antiviral, antibacterial, hepatoprotective, anti-diabetic, hypolipedemic, antithrombotic and hypotensive activities. Depending on the species, varieties, and the stage of development of the fruiting body, the crude protein content of edible mushrooms ranges from 10% to 35% of dry weight (DW). The dry weight recommended to maintain an optimal nutritional balance in a man weighing 70 kg is 100- 200 g.

Mushrooms are richer in proteins than most vegetables. Specifically, the amount of essential amino acids in mushroom proteins ranges from 30 to 50g/100g protein DW, from which the most important ones are glutamic acid (130–240 mg/g protein DW%), aspartic acid (91–120 mg/g protein DW %) and arginine (37–140 mg/g protein DW%). Besides these, the two unusual amino acids γ-amino butyric acid (GABA), a non- essential amino acid, and ornithine, known for their peculiar physiological activities, have also been found. Similar to proteins, the carbohydrate content in the fruiting bodies comprising of monosaccharides (eg sugars), oligosaccharides (eg trehalose and non-starch polysaccharides), and small amounts of sugar alcohol, such as mannitol and trehalose serve as 50 to 65% on dry weight.

In comparison with carbohydrates and proteins, mushrooms are low in lipids (less than 5% DW). With a total lipid content of 20 to 30 g kg-1 DM, mushrooms contain unsaturated fatty acids, such as linoleic and oleic acids and tocopherol. Whereas tocopherol is an important antioxidant, the linoleic acid has been mentioned to exhibit anti-carcinogenic effects on almost all stages of tumorigenesis in breast, prostate, and colon cancers. The vitamin content of five types of mushrooms are presented in Table 1.

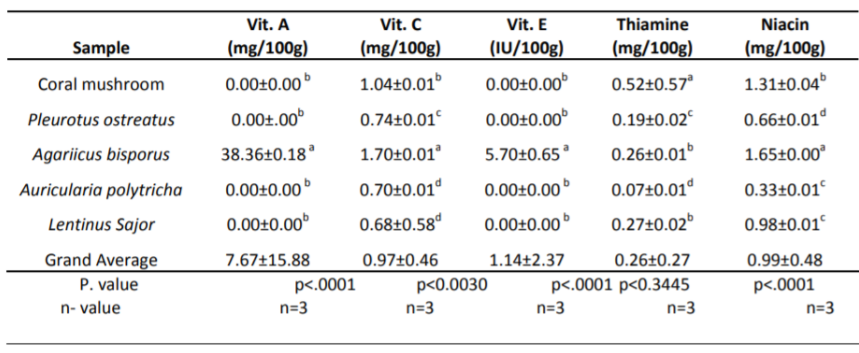
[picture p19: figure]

Fig 1: The concentration of vitamins in five species of commercial mushrooms (Afiukwa, Celestine & P.C., Ugwu & Okoli, S.O. & Idenyi, John & Ossai, Emmanuel. (2013). Contents of some vitamins in five edible mushroom varieties consumed in abakaliki metropolis, Nigeria. Research Journal of Pharmaceutical, Biological and Chemical Sciences. 4. 805-812.)

Besides the vitamins mentioned in the table, mushrooms represent a good reservoir of vitamins B and D. When exposed to UV light, fungal sterol, ergosterol, is converted to vitamin D2 through a series of photochemical and thermal reactions, in amounts greatly higher than that of daily requirements.

### Cultivation of mushrooms: between science and art

As we have shown in the previous section, mushrooms provide a large variety of nutrients necessary for the good functioning of the human body. Besides their obvious multi-functional medical properties, the fast growing period and the capacity to thrive in spatially-restricted areas may make the spore- bearing fruiting body of fungus the ideal consumable entirely grown on a spaceship.

Annually, the mushroom cultivation market is estimated to be $16.65 billion in 2020 and is expected to reach $22.78 billion by 2028. The popularity of the commercial species, including Pleurotus ostreatus, is attributed to the rapid growing rates, being ready for harvest after 7 days. Moreover, in a controlled environment, due to its high saprophytic colonisation ability, the entire cultivation is more straightforward as the substratum is fastly penetrated.

### Environmental conditions

In comparison with the natural requirements, the commercially-produced mycelium should benefit from higher optimal air temperatures. As noticed in the graph, the acceleration of growth occurs between 15 and 20 ℃.

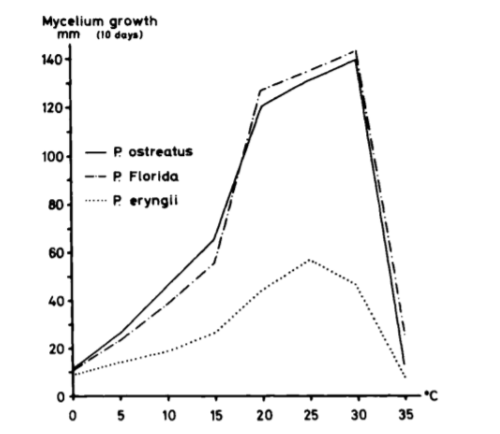
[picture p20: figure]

Figure 2: The mycelium growth as a function of temperature (ZADRAŽIL, F., 1978. Cultivation of pleurotus. The Biology and Cultivation of Edible Mushrooms, pp.521–557)

Another reason for which agriculture focuses on the Pleurotus group is that the mushrooms can flourish on artificial substrate on synthetic materials as long as it is associated with the corresponding nutrient solution. The table below shows the concentrations of the nutrients necessary to support mycelium development.

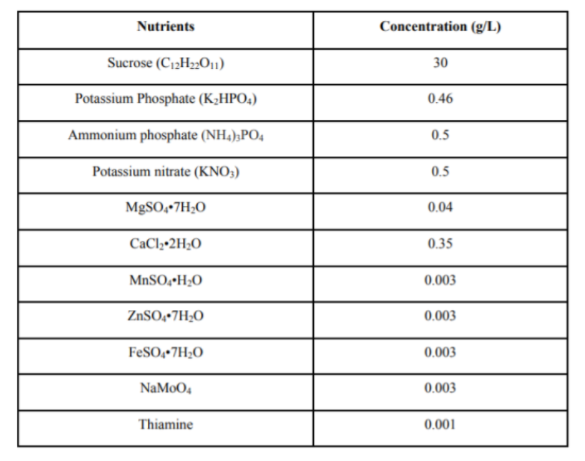
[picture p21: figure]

Fig 3: Nutrients and correspondent concentrations for mycelium growth (Prof. Chandra Madramootoo, “Mycelium and Mushroom Production Using a Hydroponic Porous Tube Nutrient Delivery System”, Department of Bioresource Engineering, McGill University, Macdonald Campus, April 2018)

Regarding the amount of oxygen, discussion is more complex considering that the development stages differ in oxygen requirements: mycelial growth demands semianaerobic conditions whereas carpophores develop under the presence of oxygen.

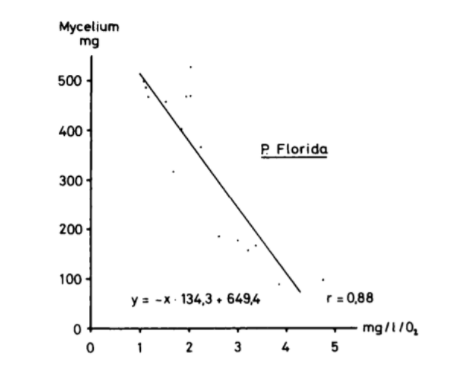
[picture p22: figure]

Fig 4: The mycelium growth as a function of oxygen concentration (ZADRAŽIL, F., 1978. Cultivation of pleurotus. The Biology and Cultivation of Edible Mushrooms, pp.521–557)

PH is another parameter which should be taken into account when cultivating mushrooms as acid (pH= 4) and basic (pH= 7) settings inhibit the growth. However, considering that the mycelium growth lowers the pH values quickly, slightly higher values than the optimum can also be accepted as well.

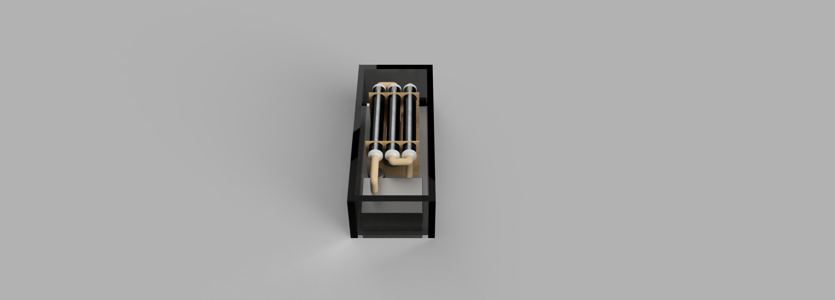
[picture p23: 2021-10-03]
CAD/Screenshots/FunGuyDesign_2021-Oct-02_08-36-13PM-000_CustomizedView49979277067.png

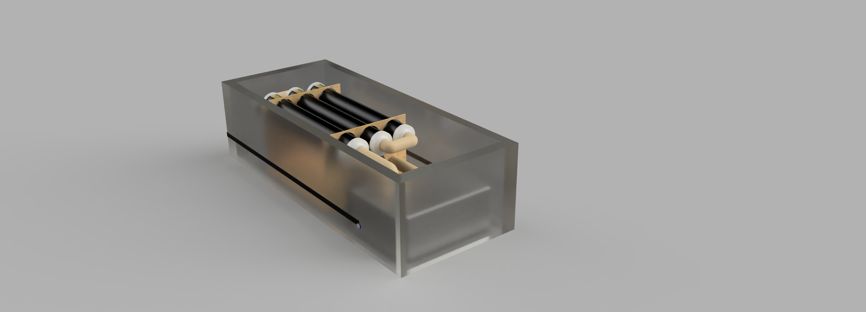
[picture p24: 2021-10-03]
CAD/Screenshots/FunGuyDesign_2021-Oct-02_08-05-37PM-000_CustomizedView10638262931.png

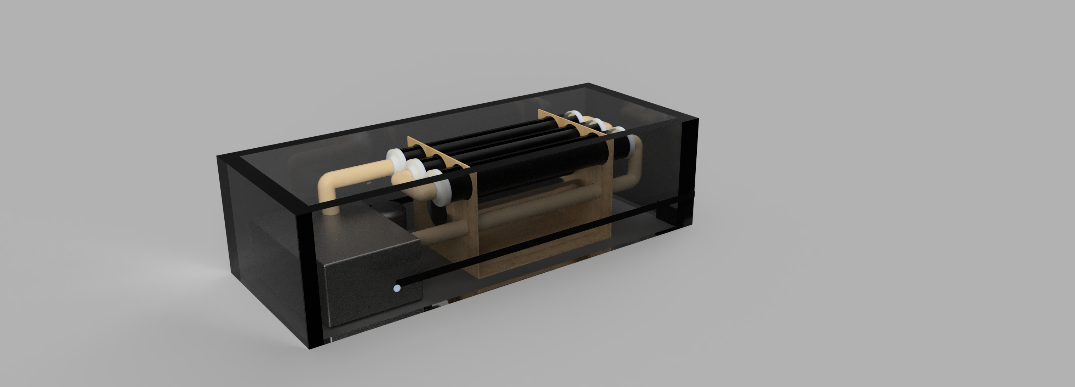
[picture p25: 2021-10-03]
CAD/Screenshots/FunGuyDesign_2021-Oct-02_08-18-01PM-000_CustomizedView2897051753.png

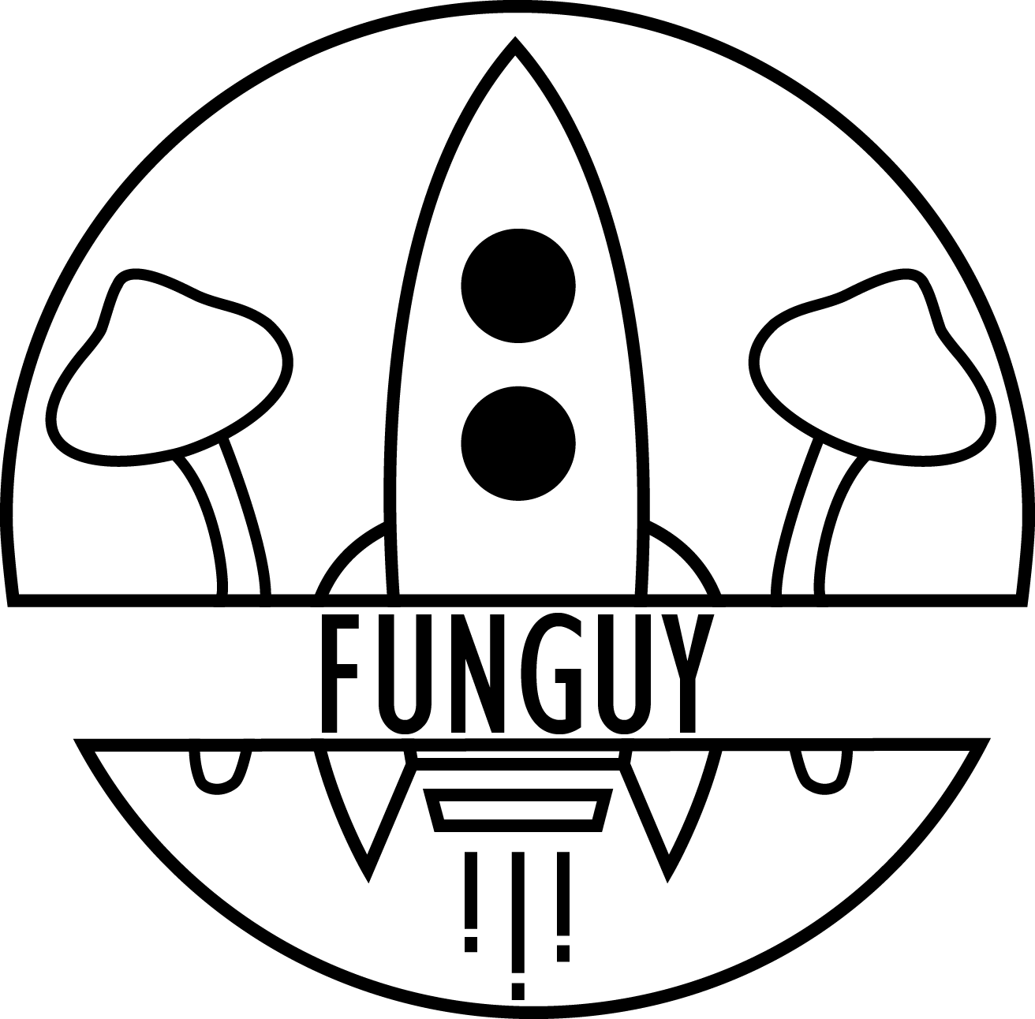
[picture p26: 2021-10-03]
Assets/8Asset 2@2x.png

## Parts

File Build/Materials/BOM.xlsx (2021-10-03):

Item | Description | Quantity | Cost | Bought
Ceramic tubes |  |  |  | Yes
Acrylic Sheets | Sheet of acrylic for frame | 4
PVC pipes | 2.5cm |  |  | Yes
Aquarium Heater |  |  |  | Arriving
Aquarium Pump |  |  |  | Arriving
Humidifier
Environmental sensor |  |  |  | Arriving
Resoviour (tank) | Food safe? Tank for storing nutrient dist |  |  | Yes
Chemical substances (see doc) | https://hydrobuilder.com/nutrients-and-fertilizer/hydroponic-system-nutrients.html?dir=asc&order=price
Substrate | https://mycotown.com/shop/500ml-mushroom-grow-tub/ |  |  | Yes
Cultures | https://mycotown.com/shop/blue-oyster-liquid-culture/ |  |  | Yes
Silicone Adhestive | For sealing of tank |  |  | Yes
Insulation | 40mm? Look into U values of insulation, how thick do we need
UV light
LED light
ABS pipe | For surrounding substrate |  |  | Yes
Rubber O rings

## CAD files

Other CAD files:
CAD/FunGuyDesign v1.f3d
CAD/PipeConnector v7.f3d
